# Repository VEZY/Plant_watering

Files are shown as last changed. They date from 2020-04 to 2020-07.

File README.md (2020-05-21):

# 🌊🌳 Autonomous plant watering system 

## Introduction

This project presents a smart autonomous plant watering system. The system is autonomous in energy using a 12v battery and a solar panel, and water the plant when the right conditions are all set, with a well thought (I hope) fail-proof system. It is smart because it communicates with the user(s) through the Telegram app.

The steps followed by the system are as follows:
- the soil water content is always monitored;
- if the soil water content is below a certain value (`max_soil_moisture`), the system:
  * (🔔) checks the water tank is not empty (and during) the watering event to avoid any damage to the pump running dry;
  * (🔔) checks the minimum water period between two watering events is exceeded. This is done to avoid watering the plants too many times during the day (better have a little dryness at some point), and to add some safety in case the soil moisture sensor is broken;
  * (🔔) start the irrigation ;
  * stops the irrigation whenever:
    + (🔔) the soil water content reaches a certain value (`max_soil_moisture`) or;
    + (🔔) the water tank is empty, in which case irrigation will resume as soon as it is filled again, or;
    + (🔔) the watering duration exceeds the maximum duration allowed for each watering event (`watering_max_time`). The aim here is to avoid running the pump until the water tank is empty if there is a leak in the system that would prevent the soil moisture to increase;
- (🔔) checks that plants are watered at least every given period of time (`max_wo_water`), to avoid them to die if e.g. the soil moisture sensor is broken and return always high values ;

The user is notified by Telegram messages at every important step (denoted 🔔). The user can also trigger manually an irrigation event from Telegram, even if the soil water content is higher than the given value (`max_soil_moisture`). It is also possible to turn the whole system ON and OFF, ask if the system is up and running, or ask the current value of the soil water content.

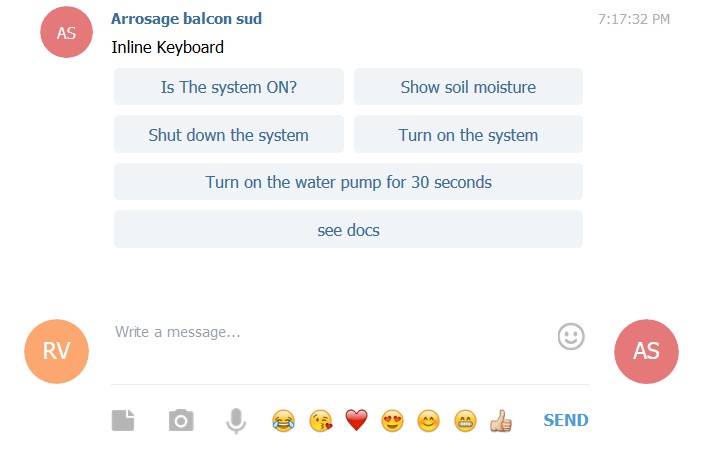
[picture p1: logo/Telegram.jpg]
Telegram snapshot


> When you go out for vacations, simply add a friend to the Telegram group so they know when to visit your house to fill up the water tank!

## Set up yours

To reproduce this project, you'll need some tools, some material, and the code from this project.

### Code

To get the code from this project, either clone it (or better, fork it) using GIT, and if you don't know what GIT, clone and fork means, simply download it on your computer using [this link](https://github.com/VEZY/Plant_watering/archive/master.zip) 😺.

Then, configure it to your needs !

To use Telegram, the NodeMCU needs to be connected to the internet. I did it using its WIFI module and my home WIFI.
To configure your own connection, open the `plant_watering.ino` script in Arduino IDE, and fill-in the missing values for your wifi credentials (I'm assuming you have WiFi):

```c
String ssid  = "xxxxx"; // Name of your Wifi
String pass  = "xxxxx"; // Wifi Password
```

Then, we'll set up a Telegram bot, which is an user account a little like you have, but actually run by a robot (your NodeMCU). To do so, follow the steps described [here](https://core.telegram.org/bots#6-botfather). In few words:
- Open Telegram (and connect with your account);
- Create a new bot:
 * Search `BotFather` in your contacts (type it in the search bar), and open a conversation with it (as you'd do with any new contact);
 * Type `/newbot` in the conversation (watch for the case and include the `/`!)
 * Name your bot as you want, but end it with "bot" (e.g. "watering_balcony_bot");
 * `Botfather` gives you a bot token, keep it very secret (don't share it using GIT!!), we'll use it in few steps;
 * Search it in your contacts, and send it this message: `/start`
 * Copy the token returned by `Botfather` and paste it on your `plant_watering.ino` script here:
```c
String token = "xxxxxx:xxxxxxxxxxxxxxxxxxxxxxx"; // Telegram bot token
```

Your bot is now alive !

To give it the ability to communicate with you, it needs to know your conversation ID. Because we want to be able to share what the bot is saying with other people in case we go out in vacation, I prefer to create a group chat instead. So create one (`New Group`), add your bot by searching its name, and add a third bot named `IDBot` temporarily. Then name your group chat as you want.
Open your group chat, and type `/getgroupid`. IDBot will return a number such as -xxxxxxxxx (don't forget the minus when you copy it!), that's your group chat ID!
> you can also ask `/getid` to get your personal ID, so your bot will send messages directly to you instead (not sending it to the group)

Copy the ID, and paste it on your `plant_watering.ino` script here:
```c
int chatID = -000000000; // This the ID of your group chat
```
> Paste the `/getid` here instead if you want the bot to send messages directly to you

Then, remove IDBot from your group just in case (we don't want any data leaked).

For the last step, you'll need to install the `CTBot` and `ArduinoJson` libraries. To do so, type `ctrl+maj+I`, search `CTBot`, and search for `CTBot by Stefano Ledda`, and click install. Then repeat for `ArduinoJson`, and search for `ArduinoJson by Benoit Blanchon`, but install the version 5.13.5 for now because `CTBot` is not compatible with the sixth version yet (you can check [here](https://github.com/shurillu/CTBot) if there are any changes).

And that's it, your code is ready !
Now you can upload it to the NodeMCU! If there are some errors, check that you selected NodeMCU 1.0 as the board type, and that you use the right version for your libraries.

### Tools

The tools are very simple, I used for this project:
- A soldering iron + tin (e.g. 220V 60W);
- A multimeter (mine is a TackLife DM01M);
- A flat screwdriver (tiny is better);
- Cutting pliers;

If you have them you can also add some wire strippers, but they are not indispensable.

### Material

Here is a list of the products used to build the system. I must say that I don't receive any incentives from Amazon, from which all products were bought.

To control the system:
- [NodeMCU board (ESP8266)](https://www.amazon.fr/gp/product/B0754HWZSQ/ref=ppx_od_dt_b_asin_title_s02?ie=UTF8&psc=1) for the brain, 17.99€
- [Relay module](https://www.amazon.fr/gp/product/B07GRW83FR/ref=ppx_od_dt_b_asin_title_s02?ie=UTF8&psc=1), 11.99€
- [120 prototyping jumper wires](https://www.amazon.fr/gp/product/B01JD5WCG2/ref=ppx_yo_dt_b_asin_title_o05_s00?ie=UTF8&psc=1), 6.99€  -> prototyping
- [3 breadboards](https://www.amazon.fr/gp/product/B06XKZYFYN/ref=ppx_yo_dt_b_asin_title_o05_s00?ie=UTF8&psc=1), 8.99€ -> prototyping
- [Waterproof box](https://www.amazon.fr/gp/product/B00HW0OMKU/ref=ppx_yo_dt_b_asin_title_o05_s00?ie=UTF8&psc=1), 10.99€
- [525 pieces resistors kit](https://www.amazon.fr/gp/product/B071LHFQKD/ref=ppx_yo_dt_b_asin_title_o03_s01?ie=UTF8&psc=1), 10.99€
- [Printed PCB](https://www.amazon.fr/gp/product/B07G5CRQXK/ref=ppx_yo_dt_b_asin_title_o02_s00?ie=UTF8&th=1) with connections similar to a breadboard, 9.27€
- [Electrical stranded wires 20, 22 or 24 AWG](https://www.amazon.fr/gp/product/B07G72DRKC/ref=ppx_yo_dt_b_asin_title_o01_s00?ie=UTF8&th=1) depending on your preference (20 is more solid but need to be reduced for some connections, 22 is good, 24 is cheaper), 18.99€

For the autonomy in energy:
- [12V Battery](https://www.amazon.fr/gp/product/B009D0KFOO/ref=ppx_yo_dt_b_asin_title_o06_s00?ie=UTF8&psc=1), 21.90€
- [10W wp 12V monocrystalline solar panel](https://www.amazon.fr/gp/product/B007HAZY8Y/ref=ppx_yo_dt_b_asin_title_o05_s02?ie=UTF8&psc=1), 23.90€
- [12/24V charge controller](https://www.amazon.fr/gp/product/B071ZZ2S84/ref=ppx_yo_dt_b_asin_title_o05_s02?ie=UTF8&psc=1), 13.99€

For the water tank:
- [12V water pump](https://www.amazon.fr/gp/product/B07NPN5XBS/ref=ppx_yo_dt_b_asin_title_o04_s00?ie=UTF8&psc=1), 16.99€
- [DC male/female connector](https://www.amazon.fr/gp/product/B07BPSCNSM/ref=ppx_yo_dt_b_asin_title_o03_s00?ie=UTF8&psc=1) (to connect the pump), 6.99€

The sensors:
- [Water level floater](https://www.amazon.fr/gp/product/B01MTYPK9I/ref=ppx_yo_dt_b_asin_title_o05_s02?ie=UTF8&psc=1), 7.99€
- [Capacitive soil moisture sensor](https://www.amazon.fr/gp/product/B07WCB3GCB/ref=ppx_od_dt_b_asin_title_s02?ie=UTF8&psc=1), 9.49€
- some nail polish for waterproofing the soil moisture sensor, 7.99€;

And the irrigation system:
- [Irrigation system](https://www.amazon.fr/gp/product/B07MSJSMXK/ref=ppx_yo_dt_b_asin_title_o05_s01?ie=UTF8&psc=1), 22.97€

For a total of 237.40€. That's not cheap!
But keep in mind that it's still cheaper than a pre-built system, and with a lot more capabilities! Also, some parts are only for prototyping (15.98€), and I purchased many components in groups of several pieces for other projects, e.g. 525 resistors is a crazy amount 🤪, you don't need 3 NodeMCU boards, nor 6 relays for this project.

### Assembly

You can find the assembly of the parts using [Fritzing](https://fritzing.org/home/) to open [the Fritzing project](Fritzing_project.fzz) in this repository. Here is a view of the whole schematic:

Breadboard view

> NB: the NodeMCU is connected to the solar charge controller by a USB cable (the one in the schematic does not have one). See the [Material](#material) section for an example of a solar charge controller with a USB.

I made all custom parts available in the [fritzing](https://github.com/VEZY/Plant_watering/fritzing_parts) folder (all can be found on the internet except the water floater because I made it).

## Acknowledgements

I would like to acknowledge my wonderful partner that let me do this during the weekends! And of course all the makers that made the project possible, such as @shurillu for the super [`CTBot`](https://github.com/shurillu/CTBot) library, EstebanP27 for his [tutorial](https://www.instructables.com/id/Smart-Plant-Watering-Using-ThingSpeaks-and-Powered/) from which I learned a lot for this project! I would also like to thanks [svgrepo](https://www.svgrepo.com) from which I used SVGs as a basis for the logo.

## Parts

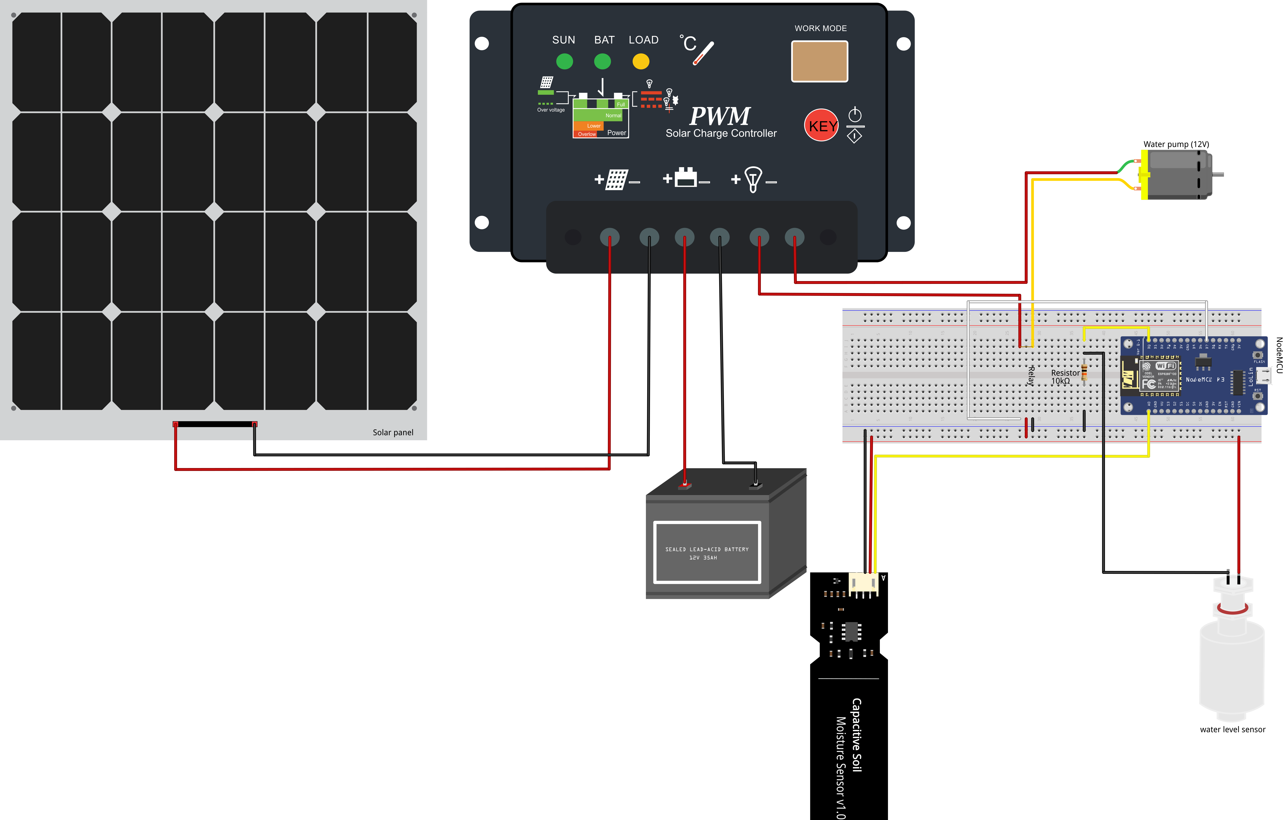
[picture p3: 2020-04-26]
fritzing/Plant_watering_components.png

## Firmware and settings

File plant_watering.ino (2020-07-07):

//Including the Telegram library for communication: 
#include "CTBot.h"

// ------- Telegram config --------
String ssid  = "xxxxx"      ; // Wifi name
String pass  = "xxxxx"; // Wifi Password
String token = "xxxxxx:xxxxxxxxxxxxxxxxxxxxxxx"   ; // Telegram bot token
int chatID = -000000000; // This the ID of our group chat for the plants

// Instantiate a bot object:
CTBot myBot;
CTBotInlineKeyboard myKbd;  // custom inline keyboard object helper

#define IS_SYSTEM_ON_CALLBACK  "isSystemON"   // callback data sent when "Is The system ON?" button is pressed
#define SOIL_MOISTURE_CALLBACK "soilMoisture" // callback data sent when "Show soil moisture" button is pressed
#define SYSTEM_OFF_CALLBACK "systemOFF"       // callback data sent when "Shut down the system" button is pressed
#define SYSTEM_ON_CALLBACK "systemON"         // callback data sent when "Turn on the system" button is pressed
#define PUMP_ON_CALLBACK "pumpON"             // callback data sent when "Turn on the water pump" button is pressed

#define Bot_mtbs 1000 //mean time between scan messages
#define Bot_mtbs_2 86400000 //mean time between messages for "no plant wattering since X days"
long Bot_lasttime;   //last time messages' scan has been done

#define interval 500 // Interval between readings

// Define pins: 
#define relay 13
#define soil_moisture  A0
#define tank_floater  16

// State of the whole system:
bool system_on = true;

// State of the pump in manual mode: 
bool pump_manual_state = false;
int manual_watering_duration = 30000; // Manual watering duration

// Floater in the water tank: 
int water_level = 2;
bool is_level_change = false; // Keep trace of a change in tank level
int prev_water_level = 2;     // To keep trace of the water level from the previous loop execution

// Soil Moisture sensor: 
int moisture = 0;             // Initializing moisture to 0
int moisture_perc = 0;        // Moisture in %
const int AirValue = 750;    // Driest value -> air value
const int WaterValue = 280;  // Wettest value -> water value

// Timer to avoid wattering for too long: 
int watering_max_time = 600000;       // Maximal time for one wattering event (10 minutes)
long watering_interval_min = 7200000L; // Minimal time to wait before two waterring events (2 hours here)
long last_watering_start = 0.0 ;      // time since the waterring event as been started
long last_watering_end = -watering_interval_min; // time since the last waterring event as been ended
// NB: initialized at -watering_interval_min to be able to start wattering at startup.
long max_wo_water = 345600000L; // Maximum days without wattering until notification to say there's probably an issue with the system


#define min_soil_moisture 40         // Min soil moisture (trigger when below):
bool unexpected_watering_end = false;// Flag unexpected end of a watering event


void setup() {
  // Set up the connexion to see the values from the moisture sensor:
  Serial.begin(9600);
  // Set the pin modes: 
  pinMode(relay, OUTPUT);
  pinMode(tank_floater, INPUT_PULLUP);
  
  Serial.println("Starting TelegramBot...");
  // myBot.setMaxConnectionRetries(15); // try 15 times to connect to the specified SSID (mySSID)
  // connect the ESP8266 to the desired access point
  myBot.wifiConnect(ssid, pass);

  // set the telegram bot token
  myBot.setTelegramToken(token);
  
  // check if all things are ok
  if (myBot.testConnection()){
    Serial.println("\nTelegram connection test: OK");
  } else {
    Serial.println("\nTelegram connection test: problem");
  }

  // Inline keyboard for Telegram (set the buttons):
  // Add a query button to the first row of the inline keyboard to know if the system is ON:
  myKbd.addButton("Is The system ON?", IS_SYSTEM_ON_CALLBACK, CTBotKeyboardButtonQuery);
  // Add another query button to the first row of the inline keyboard to get the soil moisture:
  myKbd.addButton("Show soil moisture", SOIL_MOISTURE_CALLBACK, CTBotKeyboardButtonQuery);
  // add a new empty button row
  myKbd.addRow();
  // add a query button to the second row of the inline keyboard for setting the system OFF:
  myKbd.addButton("Shut down the system", SYSTEM_OFF_CALLBACK, CTBotKeyboardButtonQuery);
  // add another query button to the second row of the inline keyboard for setting the system ON:
  myKbd.addButton("Turn on the system", SYSTEM_ON_CALLBACK, CTBotKeyboardButtonQuery);
  // add a new empty button row
  myKbd.addRow();
  // add another query button to the third row of the inline keyboard for setting the water pump ON:
  myKbd.addButton((String)"Turn on the water pump for "+(manual_watering_duration/1000)+" seconds", PUMP_ON_CALLBACK, CTBotKeyboardButtonQuery);
  // add a new empty button row
  myKbd.addRow();
  // add a URL button to the fourth row of the inline keyboard for documentation:
  myKbd.addButton("see docs", "https://github.com/shurillu/CTBot", CTBotKeyboardButtonURL);
}

void loop() {
  // Read the input soil moisture on analog pin A0:
  moisture = analogRead(soil_moisture);
  moisture_perc = map(moisture,WaterValue,AirValue,100,0);
  
  // Read the input from the float sensor in the water tank:
  water_level= digitalRead(tank_floater);
  TBMessage msg; // Store telegram message

  // Check if there is an incoming message from Telegram:
  if (myBot.getNewMessage(msg)) {
    // check what kind of message was received
    if (msg.messageType == CTBotMessageText) {
      // received a text message
      if (msg.text.equalsIgnoreCase("Show keyboard")) {
        // the user is asking to show the inline keyboard --> show it
        myBot.sendMessage(msg.sender.id, "Inline Keyboard", myKbd);
      } else {
        // the user write anithing else --> show a hint message
        myBot.sendMessage(msg.sender.id, "Try 'Show keyboard' to get the keyboard options.");
      }
    } else if (msg.messageType == CTBotMessageQuery) {
      // received a callback query message
      if (msg.callbackQueryData.equals(IS_SYSTEM_ON_CALLBACK)) {
        // Say if the system is running: 
        myBot.endQuery(msg.callbackQueryID, "The system is up and running!", true);
      } else if (msg.callbackQueryData.equals(SOIL_MOISTURE_CALLBACK)) {
        // Return the soil moisture as a popup message
        myBot.endQuery(msg.callbackQueryID, (String)"Soil Moisture : "+moisture_perc+"%"+"("+moisture+")",true);
      } else if (msg.callbackQueryData.equals(SYSTEM_OFF_CALLBACK)) {
        // Turn off the system.
        system_on = false;
        myBot.endQuery(msg.callbackQueryID, "Shutting down the system");
      } else if (msg.callbackQueryData.equals(SYSTEM_ON_CALLBACK)) {
        // Return the soil moisture as a popup message
        system_on = true;
        myBot.endQuery(msg.callbackQueryID, "Re-starting the system");
      } else if (msg.callbackQueryData.equals(PUMP_ON_CALLBACK)) {
        // Turn on the pump manually.
        pump_manual_state = true;
        myBot.endQuery(msg.callbackQueryID, (String)"Starting manual watering for "+(manual_watering_duration/1000)+" second");
      }
    }
  }

  // Start of the actual program for the system (only if system_on is ON): 
  if (system_on){
    
    if (water_level == prev_water_level) {
      is_level_change = false;
    } else {
      is_level_change = true;
    }
  
    if (water_level == HIGH) {
      // If there is water in the tank...
      // Print the moisture to the console: 
      Serial.print((String)"Soil Moisture : "+moisture_perc+"%"+"("+moisture+")"+"\n");
  
      // If tank was just refilled: 
      if (is_level_change) {
        // Sending a message via Telegram (only if it wasn't said already, and it didn't change just before)
        if ((millis() > Bot_lasttime + Bot_mtbs))  {
          myBot.sendMessage(chatID, "Thank you for refilling the water tank !");
          Bot_lasttime = millis();
        }
      }

      Serial.print((String)"last_watering_end  : "+last_watering_end +", watering_interval_min : "+watering_interval_min+"\n");

      if ((((long(millis()) > last_watering_end + watering_interval_min)||unexpected_watering_end) && (moisture_perc <= 30)) || pump_manual_state) {

        // /!\ START WATERING /!\
        // NB: watering can only start after a minimum given period of time (watering_interval_min), or if it terminated unexpectedly just before;
        // or if the user request a manual activation (pump_manual_state).
        
        last_watering_start= millis(); // Record the time of watering start

        // Resetting the flag for unexpected end of watering to false when entering the watering (if stopped because the tank was empty):
        unexpected_watering_end = false;
        
        myBot.sendMessage(chatID, "Starting plant wattering !");

        Serial.print((String)"Entering watering loop. Moisture : "+moisture_perc+", min_soil_moisture : "+min_soil_moisture+"\n");
        
        while ((moisture_perc <= min_soil_moisture) || pump_manual_state) {

          // Check if there is water in the tank:
          water_level= digitalRead(tank_floater);
          
          Serial.print((String)"water_level : "+water_level+"\n");

          if(water_level == LOW){
            // If there is no more water in the tank during a watering event, stop the pump, and stop the event.
            digitalWrite(relay, LOW);
            myBot.sendMessage(chatID, "Hu-ho, I emptied the water tank during plant watering, please re-fill!");
            // NB: not using `last_watering_end= millis();` here because we want to continue the plant watering whenever the tank is re-filled

            // Flag the waterring as not finished so we can re-enter the loop whenever the tank is re-filled: 
            unexpected_watering_end = true;
            break;
          }          

          Serial.print((String)"last_watering_start : "+last_watering_start+", watering_max_time : "+watering_max_time+"\n");

          if(long(millis()) > last_watering_start + watering_max_time){
            // Make sure the system is not watering for more than watering_max_time, and if so, stop watering and make sure the pump is shut off.
            last_watering_end = millis();
            digitalWrite(relay, LOW);
            myBot.sendMessage(chatID, (String)"Plants were wattered during "+((millis()-last_watering_start)/1000)+" seconds but they are still thirsty. Try to set watering_max_time to a higher value");
            break;
          }

          if(pump_manual_state && (millis() > last_watering_start + manual_watering_duration)){
            // If the user request a manual waterring, water until manual_watering_duration
            last_watering_end = millis();
            pump_manual_state = false;
            digitalWrite(relay, LOW);
            myBot.sendMessage(chatID, (String)"Plants were wattered during "+((millis()-last_watering_start)/1000)+" seconds after your request.");
            break;
          }

          Serial.print((String)"Start waterring !\n");

          // If everything is OK, start watering:
          digitalWrite(relay, HIGH);
          moisture = analogRead(soil_moisture);
          moisture_perc = map(moisture,WaterValue,AirValue,100,0);
          
          last_watering_end= millis();  
          delay(500);                // 500ms delay
        }

        // Shut down the pump when wattering is finished (happens here only when soil_moisture > min_soil_moisture)
        digitalWrite(relay, LOW);
        myBot.sendMessage(chatID, (String)"Wattered the plants during "+((last_watering_end-last_watering_start)/1000)+" seconds");
      }
  
      if ((last_watering_end > (long(millis()) + max_wo_water)) && (millis() > Bot_lasttime + Bot_mtbs_2)){
        // NB: using long(millis()) because at first last_watering_end is negative and millis() is an unsigned long.
        myBot.sendMessage(chatID, (String)"Plants were not wattered since "+(max_wo_water/86400000)+" days. Please check the system.");
        Bot_lasttime = millis();
      }
    } else {
      // If there is no water in the tank, problem !!
      // Powering down the pump in case it was running:
      digitalWrite(relay, LOW);
      Serial.print((String)"Water tank empty. Please refill with water !"+"(soil Moisture : "+moisture_perc+"%)"+"\n");
  
      // Sending a message via Telegram (only if it wasn't said already, and it didn't change just before)
      if ((millis() > Bot_lasttime + Bot_mtbs) && is_level_change)  {
        myBot.sendMessage(chatID, "The water tank is empty, please refill before all plants die !");
        Bot_lasttime = millis();
      }
    }
  }
  
  // Always make sure the water pump is OFF at the end of the loop just in case:
  digitalWrite(relay, LOW);
    
  prev_water_level= water_level;
  delay(interval);    
}

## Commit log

2020-03-22 First commit: Testing relay
2020-03-22 Add functional code for Moisture sensor (with calibration) + relay + floater
2020-04-13 Add checks to not watter for too long, and not watter every too short periods
    [plant_watering.ino]
2020-04-13 Fix issues on some behaviors
    [plant_watering.ino]
2020-04-19 Add option to turn the pump on manually from Telegram
2020-04-19 Fix issue due to data type from millis() -> unsigned long but compare with negative values at start
    [plant_watering.ino]
2020-04-20 Starting assembly share using Fritzing
    [Fritzing_project.fzz]
2020-04-25 Share assembly with Fritzing project
    [Fritzing_project.fzz]
2020-05-21 Increase minimum soil water content (was too low) + add Bot_mtbs_2 to send message each day only if not wattered since last_watering_end
    [plant_watering.ino]
2020-06-01 Update maximal time for watering event (was too low) + reduce interval between watering event
    [plant_watering.ino]
